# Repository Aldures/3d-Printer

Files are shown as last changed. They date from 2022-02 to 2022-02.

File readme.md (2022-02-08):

# Tronxy X5SA Pro to TC-Bot conversion

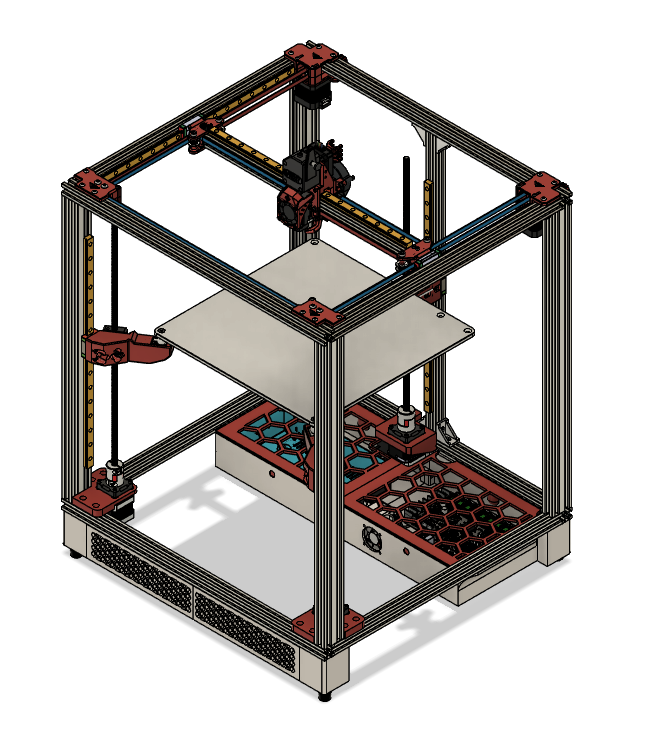
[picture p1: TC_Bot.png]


The x5sa pro is a really cheap core-xy 3d printer which is really not that bad on its own. This printer can be improved by changing some parts that were included with the kit. Most parts are clones such as the print head and extruder. This was done to reduce the overall cost of the printer. I really like how they made their linear rails however it makes it more diffcult to use Voron or RatRig print heads without some design changes which most people cannot do on their own. What I have done is have taken what I deem the best of Rat-Rig and VZ-Bot and combined integrated them to my printer. VZ-Bot gantry is good as it and no changes were made. I really like the 3-Stepper z-axis of Rat-Rig however their cad files were made with a 3030 frame in mind and had to be re-cadded to work with my X5SA Pro frame.

There are many things which need to be upraded in order to make this a better printer. I will list all changes I have made to my printer as well as all cad/stl files I made to improve printing.

|Problem Areas                                                                                      |
|---------------------------------------------------------------------------------------------------|
|clone extruder|
|clone hot end|
|24v print bed|
|no removable print surface|
|inducter auto leveling|
|not real linear rails|
|cannot drive more than 4 motors main printer board|
|raspberry pi 4 - needed for klipper |
|cheap power supply|
|mosfets/solid state switches are needed for saftey and boards protection|
|frame re-inforcements are needed to dull vibrations|
|electrical box is not bad, but power supply and computer shouldn't be in same box|
|din rails are needed to hang all electronics unders the frame|
|legs are needed to increase the height of the frame so you can hide electronics under frame|
|skirt is needed to make things pretty|
|bottom panel to hang eletronics from|
|no enclosure|

# Mods
extra parts needed to improve your printer

## Electronics
| Qte | Parts | Overview |
|-----|---|---|
|1| btt octopus v1.1 | You need a board with no less than 5 drivers. You need atleast 2 drivers for Z-axis|
|1| tmc2209 drivers | I like the ability to use sensorless endstops. |
|1| 24v Power supply | The power supply shipped with the X5SA Pro is not really good. |
|1| Raspberry Pi 4 | This is used for Klipper |

## Print head / Extruder
| Qte | Parts | Overview |
|-----|---|---|
|1| bondtech bmg extruder | I like non cloned extruders, they function better |
|1| phaetus bms print head | any hot end can be used however I tried this one and was impressed |
|1| solid state switch for hotend heater ||
|1| bltouch v3.1 | I do not like intductive probes. This gives you the choice of using any print surface. |

## Print Bed
| Qte | Parts | Overview |
|-----|---|---|
|1| 8mm mic6 Aluminum 330mm x 330mm print bed | The stock print bed on the X5SA is really thin and mine was not really flat. |
|1| 310mm x 310mm magnetic print surface | I like flexible steel PEI print surfaces ||
|1| 110v 750w 290mmx290mm silicone heat pad | Since I needed a new heater for print bed I decided to get something that heats fast. Bigger will overlap standoffs!!!|
|1| solid state switch for 110v heat pad||
|3| 450mm mgn12c linear rails | I am using a trident z-axis configuration. It's overkill, however works nicely. This mod was inspired by RATRIG but modified to fit an X5SA Pro Frame. *** Frame has to be really properly trammed, X5SA were very loose on their frame measurements.|

---------------------------------------------------------------------------------------------------------------------------------------------
---------------------------------------------------------------------------------------------------------------------------------------------

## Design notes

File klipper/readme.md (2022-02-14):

## Klipper Config

I use Klipper to control my 3d printer. It is a really nice interface which I have learned to love.
Initially I was using FLUIDD however the owner of that branch seems to have stepped away from the project
since there seemed to be some friction between MAINSAIL and FLUIDD interfaces. For this reason I have changed
to MAINSAIL. The config has not changed.

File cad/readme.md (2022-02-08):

## Fusion360 CAD files available upon request.

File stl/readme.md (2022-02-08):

## STL files for complete TC-Bot update.

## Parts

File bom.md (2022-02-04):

## What I actually bought and from where

## From ratrig
| Qte | Parts | Where |
|-----|---|---|
|1|330x330 cast aluminium build plate|ratrig|
|6|dowel pins|ratrig|
|3|magnets|ratrig|
|3|M5 threaded steel balls|ratrig|

## For Gantry
| Qte | Parts | Where |
|-----|---|---|
|2|460mm 2020 extrusion|Faztek|
|1|440mm 2020 extrusion|Faztek|

## For Z-axis
| Qte | Parts | Where |
|-----|---|---|
|1|530mm 2020|Faztek|

## From Amazon
| Qte | Parts | Where |
|-----|---|---|
|3|450mm Tr8x2 Acme Thread, 2mm Pitch, 1 Start, 2mm Lead|Amazon|
|3|TR8x2 Acme Anti Backlash Nut Block|Amazon|
|3|TR8 couplers|Amazon|

## Linear rails from Aliexpress
| Qte | Parts | Where |
|-----|---|---|
|1|400 mgn12c rail hotend x-axis gantry|Aliexpress|
|2|400 mgn12c rail y-axis gantry|Aliexpress|
|3|450 mgn12c rail for z-axis|Aliexpress|

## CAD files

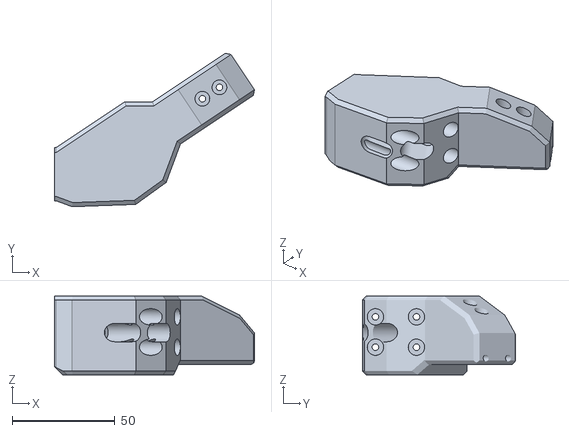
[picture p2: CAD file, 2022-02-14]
stl/right arm.stl
97.5 x 74.8 x 38.5

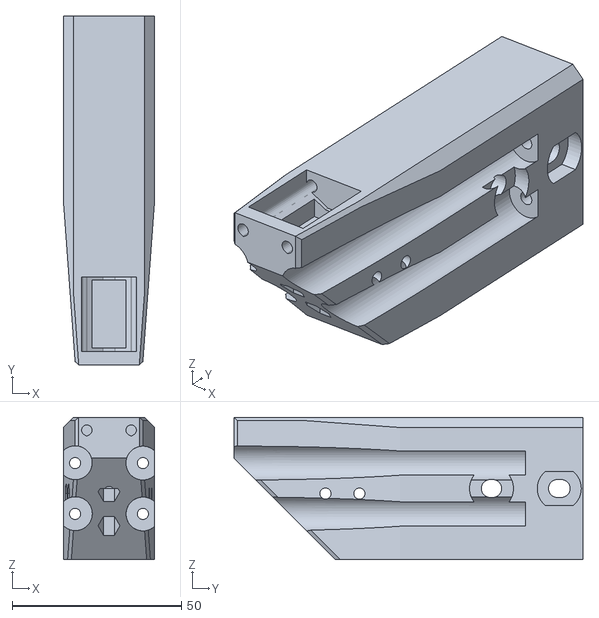
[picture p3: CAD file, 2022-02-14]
stl/rear arm.stl
27.0 x 103.0 x 42.0

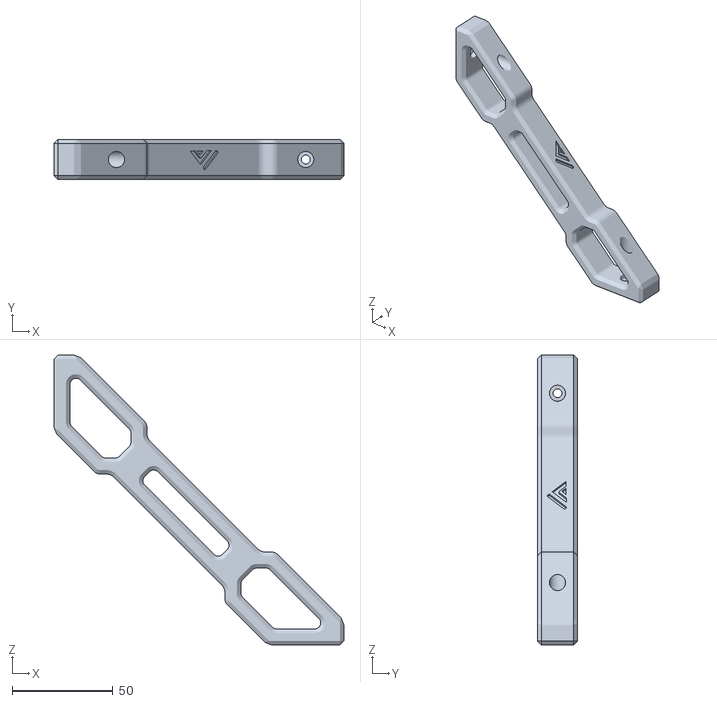
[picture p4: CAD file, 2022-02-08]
stl/Frame_Brace.stl
144.1 x 20.0 x 144.1

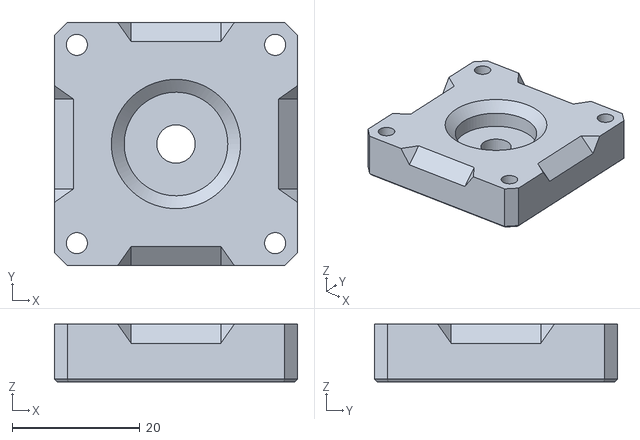
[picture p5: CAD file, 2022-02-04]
stl/pillow_block.stl
38.0 x 38.0 x 9.00

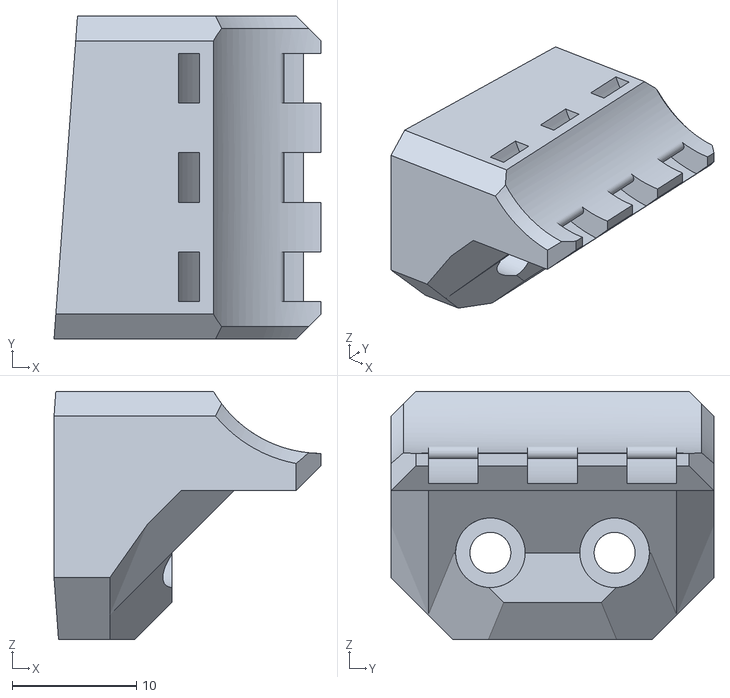
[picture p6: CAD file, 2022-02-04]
stl/bed_cable_relief.stl
21.5 x 26.0 x 20.0

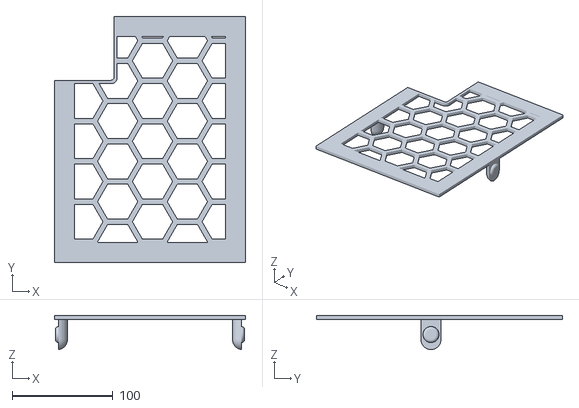
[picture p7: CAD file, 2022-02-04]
stl/lid left.stl
190.0 x 244.5 x 33.9

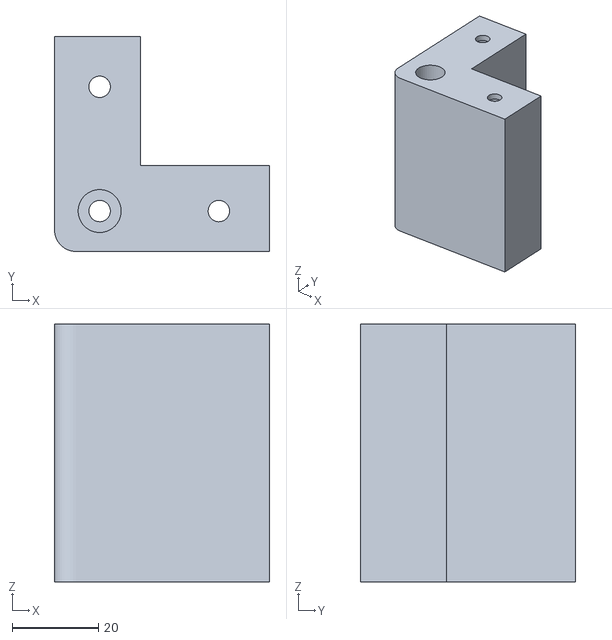
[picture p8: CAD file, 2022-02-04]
stl/leg.stl
50.0 x 50.0 x 60.0

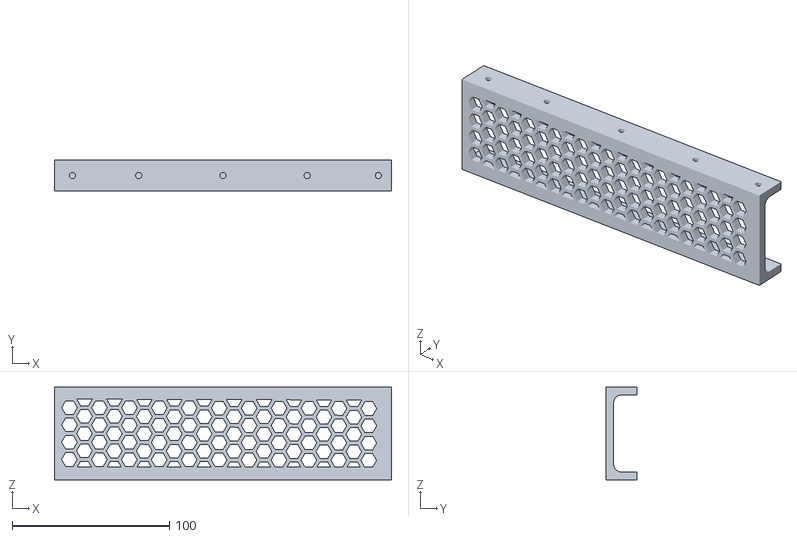
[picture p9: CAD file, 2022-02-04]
stl/front_right.stl
214.5 x 20.0 x 59.0

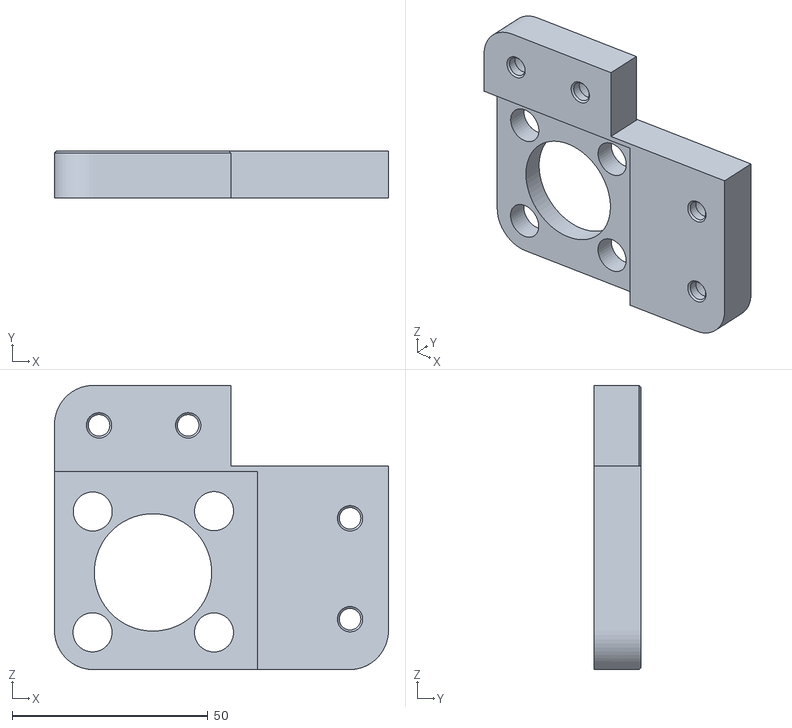
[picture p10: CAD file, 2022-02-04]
stl/bottom left motor mount.stl
85.4 x 12.0 x 72.7

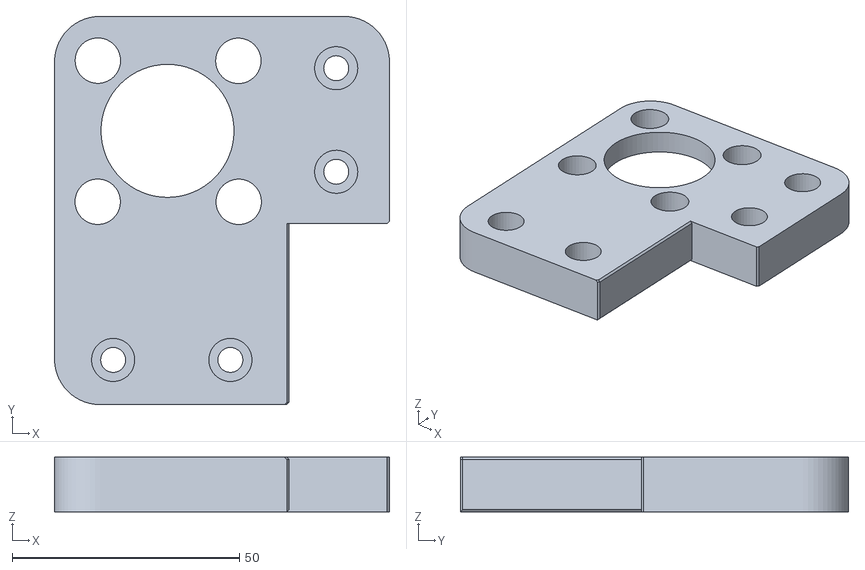
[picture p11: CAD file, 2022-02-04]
stl/bottom right motor mount.stl
73.7 x 85.4 x 12.0

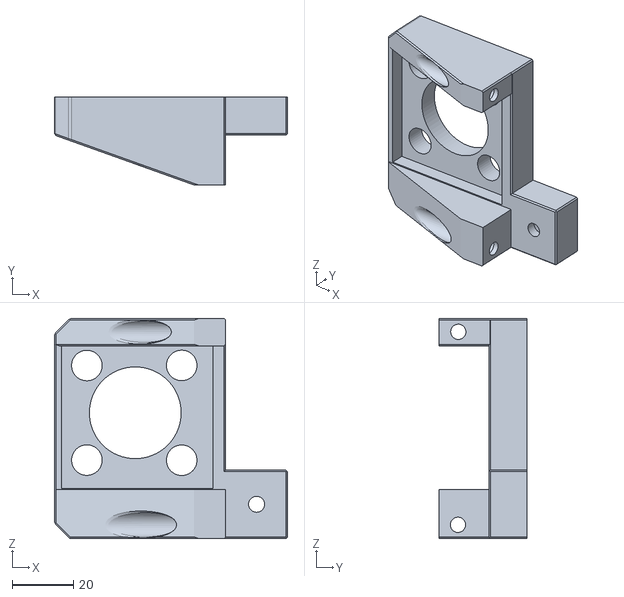
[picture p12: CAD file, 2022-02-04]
stl/back motor mount.stl
76.2 x 28.8 x 72.0

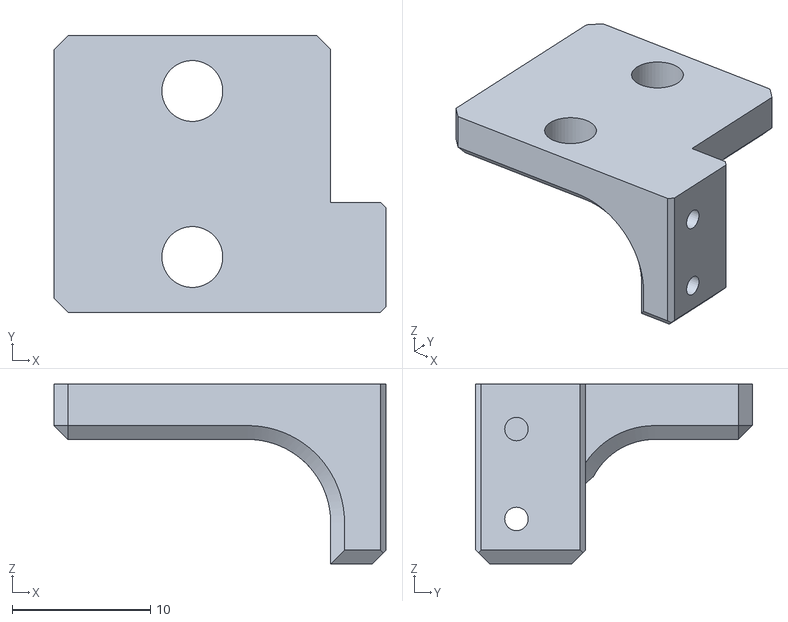
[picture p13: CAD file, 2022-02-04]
stl/y_limit_switch.stl
24.0 x 20.0 x 13.0

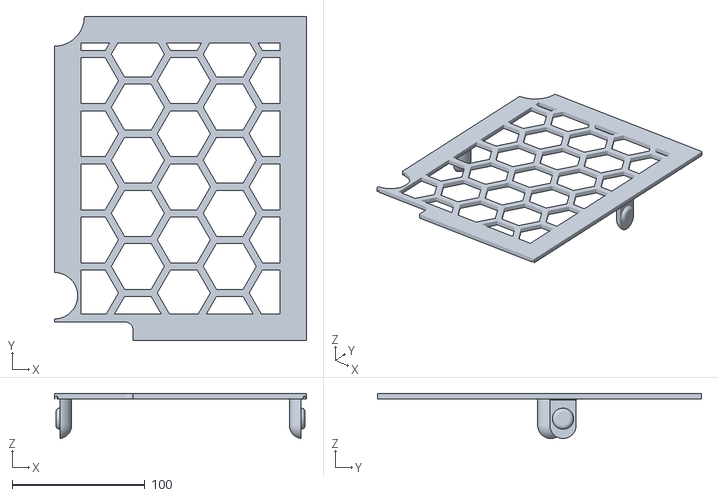
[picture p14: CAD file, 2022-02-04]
stl/lid right.stl
190.0 x 244.5 x 33.9

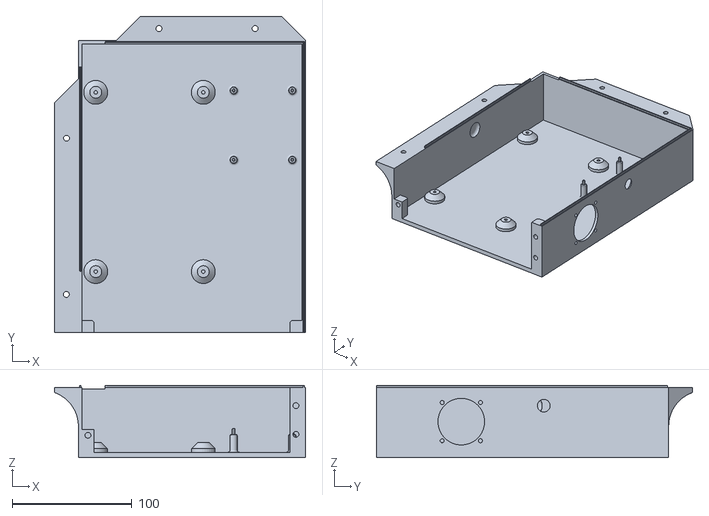
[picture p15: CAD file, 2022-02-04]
stl/case right.stl
210.0 x 264.5 x 60.5

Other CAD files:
stl/left arm.stl
stl/front_left.stl
stl/case left.stl

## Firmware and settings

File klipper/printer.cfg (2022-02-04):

## Config file inspired by Voron Design VORON2 250/300/350mm BigTreeTech OctoPus V1 TMC2209 UART config



[mcu]
serial: /dev/serial/by-id/usb-Klipper_stm32f446xx_3C0028001950534841313020-if00

[printer]
kinematics: corexy
max_velocity: 500  
max_accel: 10000    			#Max 4000
max_accel_to_decel: 10000
max_z_velocity: 10 			#Max 15 for 12V TMC Drivers, can increase for 24V
max_z_accel: 30
square_corner_velocity: 5.0

#####################################################################
# 	X/Y Stepper Settings
#####################################################################

## X Stepper on MOTOR0(B Motor)
[stepper_x]
step_pin: PF13
dir_pin: !PF12
enable_pin: !PF14
rotation_distance: 40
microsteps: 16
full_steps_per_rotation: 200  
endstop_pin: !PG6 
position_min: 0
position_endstop: 0 
position_max: 330
homing_speed: 200   #Max 100
homing_retract_dist: 5

[tmc2209 stepper_x]
uart_pin: PC4
interpolate: True
run_current: 0.8
hold_current: 0.7
sense_resistor: 0.110
stealthchop_threshold: 0

## Y Stepper on MOTOR1 (A Motor)
[stepper_y]
step_pin: PG0
dir_pin: PG1
enable_pin: !PF15
rotation_distance: 40
microsteps: 16
full_steps_per_rotation: 200  
endstop_pin: !PG9  
position_min: 0
position_endstop: 0
position_max: 330
homing_speed: 200  #Max 100
homing_retract_dist: 5

[tmc2209 stepper_y]
uart_pin: PD11
interpolate: True
run_current: 0.8
hold_current: 0.7
sense_resistor: 0.110
stealthchop_threshold: 0
 
#####################################################################
# 	Z Stepper Settings
#####################################################################

## Z1 Stepper - Front RIGHT on DRIVER 2  (Do Not use Driver 2_2 as it is a slave to Driver 2)
[stepper_z]
step_pin: PF11
dir_pin: !PG3
enable_pin: !PG5
microsteps: 16
rotation_distance: 2
full_steps_per_rotation: 200
endstop_pin: probe:z_virtual_endstop
position_min: -2
position_max: 400

[tmc2209 stepper_z]
uart_pin: PC6
run_current: 0.650
hold_current: 0.450
stealthchop_threshold: 999999

### Z1 Stepper - Front Left on DRIVER 6
[stepper_z1]
step_pin: PE2
dir_pin: !PE3
enable_pin: !PD4
microsteps: 16
rotation_distance: 2
full_steps_per_rotation: 200

[tmc2209 stepper_z1]
uart_pin: PE1
run_current: 0.650
hold_current: 0.450
stealthchop_threshold: 999999

#--------------------------------------------------

### Z2 Stepper - Rear Center on DRIVER 5
[stepper_z2]
step_pin: PC13
dir_pin: !PF0
enable_pin: !PF1
microsteps: 16
rotation_distance: 2
full_steps_per_rotation: 200

[tmc2209 stepper_z2]
uart_pin: PE4
run_current: 0.650
hold_current: 0.450
stealthchop_threshold: 999999


#####################################################################
#  Z-Tilt
#####################################################################

[z_tilt]
z_positions: 
    -40,-40
    310,-40
    205,310
points:
    75,25
    310,25
    205,310
   
speed: 500
horizontal_move_z: 5
retries: 5
retry_tolerance: 0.01

#####################################################################
# 	Bed Mesh
#####################################################################

[bed_mesh]
speed: 500
horizontal_move_z: 5
mesh_min:40,40
mesh_max:240,269
probe_count:4,4
fade_start: 1.0
fade_end: 10.0
algorithm: lagrange


#####################################################################
# 	PROBE
#####################################################################

[bltouch]
sensor_pin: ^PB7
control_pin: PB6
x_offset: -40
y_offset: 0
# @1.8 it works well but a bit tight
#z_offset: 3.500
pin_move_time: 0.4
speed: 100
samples: 2
pin_up_touch_mode_reports_triggered: False

#####################################################################
# 	Extruder - DRIVER_7
#####################################################################
[extruder]
step_pin: PE6
dir_pin: PA14
enable_pin: !PE0
microsteps: 16
gear_ratio: 50:17
rotation_distance: 22.10
nozzle_diameter: 0.400
filament_diameter: 1.750
#pressure_advance: 0.0306
#pressure_advance: 0.11745
# pressure_advance: 0.0895
pressure_advance: 0.045
pressure_advance_smooth_time: 0.040
heater_pin: PA2
sensor_type: ATC Semitec 104GT-2
sensor_pin: PF4
min_temp: 0
max_temp: 270

[tmc2209 extruder]
uart_pin: PD3
run_current: 0.800
hold_current: 0.500
stealthchop_threshold: 999999

#####################################################################
# 	Bed Heater
#####################################################################

[heater_bed]
##	SSR Pin - BED_OUT
heater_pin: PA1
sensor_type: NTC 100K MGB18-104F39050L32
sensor_pin: PF3
##	Adjust Max Power so your heater doesn't warp your bed
max_power: 1
min_temp: 0
max_temp: 120

#####################################################################
# 	Fan Control
#####################################################################

[fan]
pin: PA8
max_power: 1.0
shutdown_speed: 0
cycle_time: 0.010
hardware_pwm: False
kick_start_time: 0.100
off_below: 0.0

[heater_fan my_nozzle_fan]
pin: PE5
max_power:1.0
shutdown_speed:0
cycle_time:0.010
hardware_pwm:false
kick_start_time:0.100
off_below:0.0
heater: extruder
heater_temp: 50.0
fan_speed: 1.0


[controller_fan Electrionics]
pin: PD12
max_power:1.0
shutdown_speed:0
cycle_time:0.010
hardware_pwm:false
kick_start_time:0.100
off_below:0.0
fan_speed: 1.0
idle_timeout:60
idle_speed:0.50
heater:extruder


##################################################

########################################
# EXP1 / EXP2 (display) pins
########################################

[board_pins]
aliases:
    # EXP1 header
    EXP1_1=PE8, EXP1_2=PE7,
    EXP1_3=PE9, EXP1_4=PE10,
    EXP1_5=PE12, EXP1_6=PE13,    # Slot in the socket on this side
    EXP1_7=PE14, EXP1_8=PE15,
    EXP1_9=<GND>, EXP1_10=<5V>,

    # EXP2 header
    EXP2_1=PA6, EXP2_2=PA5,
    EXP2_3=PB1, EXP2_4=PA4,
    EXP2_5=PB2, EXP2_6=PA7,      # Slot in the socket on this side
    EXP2_7=PC15, EXP2_8=<RST>,
    EXP2_9=<GND>, EXP2_10=<5V>

# See the sample-lcd.cfg file for definitions of common LCD displays.

######################################################################
#  BigTreeTtech TFT TouchSCreen emulated 12864 mode
######################################################################

[display]
lcd_type: emulated_st7920
spi_software_miso_pin: PA6
spi_software_mosi_pin: EXP1_3
spi_software_sclk_pin: EXP1_5
en_pin: EXP1_4
encoder_pins: ^EXP2_5, ^EXP2_3
click_pin: ^!EXP1_2

[output_pin beeper]
pin: EXP1_1

######################################################################
#  Other Misc settings
######################################################################
[gcode_arcs]
resolution: .5

[safe_z_home]
home_xy_position: 165,165
speed: 50
z_hop: 5
z_hop_speed: 20

[idle_timeout]
timeout: 1800

[virtual_sdcard]
path: ~/gcode_files

[pause_resume]

[display_status]

########################################
# Tool to help adjust bed leveling screws.
# One may define a # [bed_screws] config section to enable a BED_SCREWS_ADJUST g-code command.
########################################

#### You must calibrate to use input shaper and find your own values.
#[input_shaper]
#shaper_freq_x: 38.5714
#shaper_freq_y: 36.5217

########################################
# Macros
########################################

[gcode_macro super_square]
gcode:
    G1 Z20 f8000

    G1 x10 y10 f10000
    g1 x10 y270 f10000
    g1 x300 y270f10000
    g1 x300 y10 f10000

    G1 x10 y10 f10000
    g1 x10 y270 f10000
    g1 x300 y270 f10000
    g1 x300 y10 f10000

    G1 x10 y10 f10000
    g1 x10 y270 f10000
    g1 x300 y270 f10000
    g1 x300 y10 f10000

    G1 x10 y10 f10000
    g1 x10 y270 f10000
    g1 x300 y270 f10000
    g1 x300 y10 f10000
#--------------------------------------------------------------------
[gcode_macro g29]
gcode:
    BED_MESH_CALIBRATE
    BED_MESH_OUTPUT
#--------------------------------------------------------------------
[gcode_macro START_PRINT]
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

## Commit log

2022-01-01 Create bom
2022-02-04 Create stl
2022-02-08 Updated bed holder arms.
    I moved the front z-axis rails inwards on the 2040. I also recentered the bed since I was not taking in consideration the size of the print head and was hitting the frame before I reduced the print s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
    [left arm.stl, right arm.stl]
2022-02-08 renamed back bed arm to rear arm.
    [rear arm.stl]
2022-02-08 Renamed bed_arm_back to rear_arm
    [bed_arm_back.stl]
2022-02-14 Fixed an error on front arms
    I made a booboo on the front arms while I was using Fusion360. I moved the bed 20mm forward to increase print volume and I had moved the rails to the read 2nd tslot in the 2040 rail (was using the front one which would block an enclosure). Whilst doing this I somehow screwed my cad positioning for the front arms relative to the plate. Long story short, both front arms were faulty and now they are fixed.
    [left arm.stl, rear arm.stl, right arm.stl]
